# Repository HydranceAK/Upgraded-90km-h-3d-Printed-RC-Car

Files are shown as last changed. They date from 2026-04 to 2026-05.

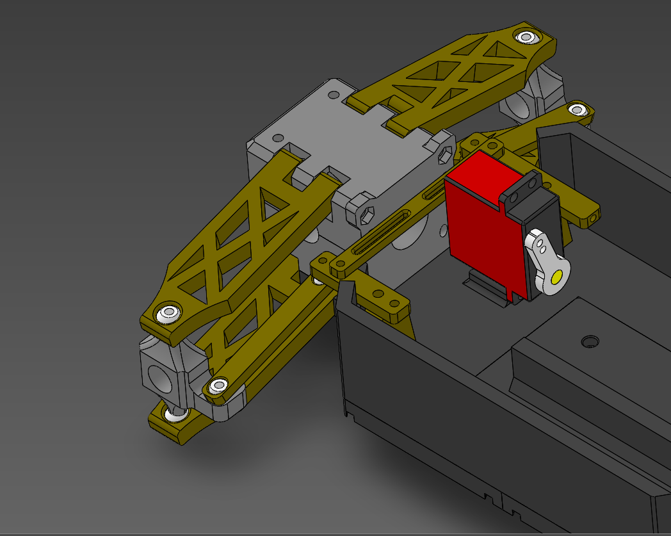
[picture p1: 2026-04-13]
Images/Screenshot 2026-04-12 164648.png

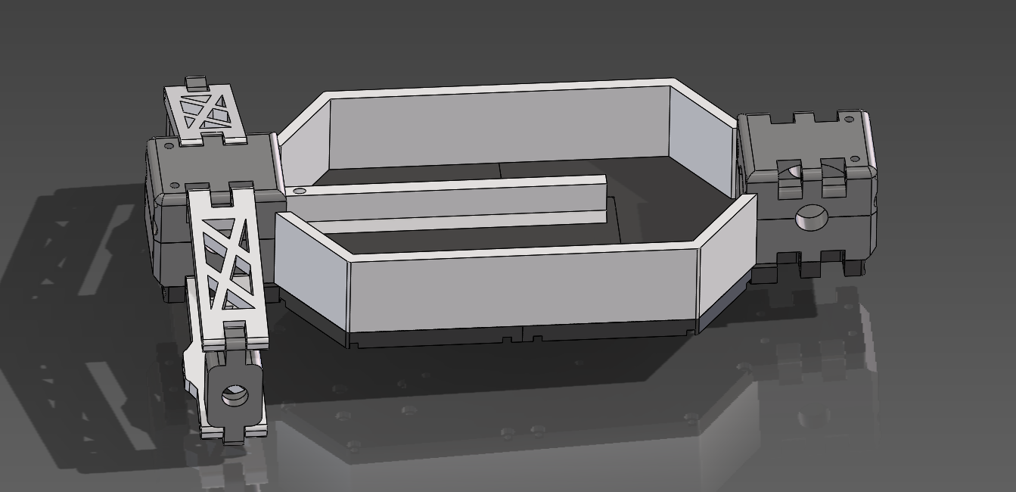
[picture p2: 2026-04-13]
Images/Screenshot 2026-04-11 005427.png

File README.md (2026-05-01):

Designed and engineered by Hydrance.

This is my final and best version of my 3d printed RC Car series. Upgraded with metal differentials, metal axles, improved suspension, 
larger frame, more space for adjustments, and an overall polished andimproved design, this will likely be my final attempt at making the perfect 3d printed RC Car.  

Im making this project because my previous build, the 60km/h RC Car, is too weak and the gears snap under high load. This makes it very annoying to drive as you need to constantly rebuild it. This new design, with the full metal drive train, should never require replacement. 

_****PROJECT STILL IN WORKS****_

Features

4WD Drivetrain

Top Speed: - 90km/h (untested as of today)

Independent Suspension

Fully metal drive train

TPU parts for flexible components (tires, dampening mounts, impact zones)

PETG parts for strong structural elements (chassis, arms, mounts)

**Printing Notes**

TPU recommended for flexible and shock-absorption components

PETG recommended for strength, heat resistance, and rigidity

Everything can be printed on Bambu Lab a1 (0.4 or 0.6 nozzle)

Hardware, electronics, and drivetrain components sourced Amazon and AliExpress

**Disclaimer**

This project is provided for personal use only.

You may not sell, redistribute, upload, or copy this design without direct permission from the creator.

I am not responsible for any damage, injury, or misuse involving this design, its assembly, or its operation.

Operate RC vehicles safely and responsibly.

**Contact**

For permissions, questions, or collaboration, contact me at:

Email: abdusamaku@gmail.com

YouTube: https://youtube.com/@HydranceYT







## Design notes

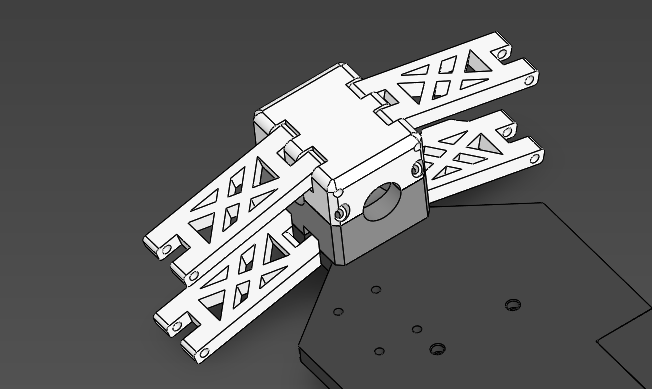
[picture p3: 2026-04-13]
Images/Screenshot 2026-04-10 205925.png

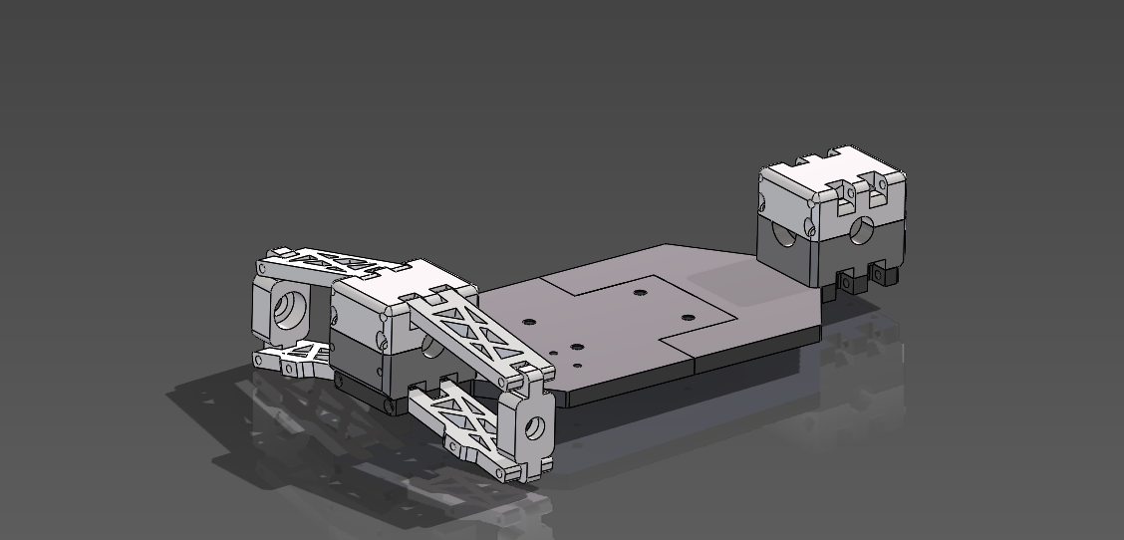
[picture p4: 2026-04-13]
Images/Screenshot 2026-04-10 213503.png

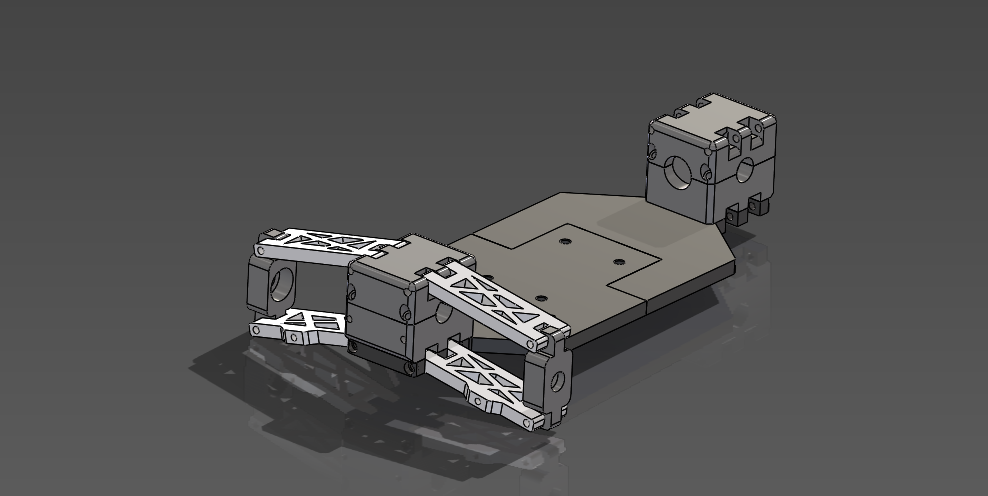
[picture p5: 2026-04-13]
Images/Screenshot 2026-04-10 213638.png

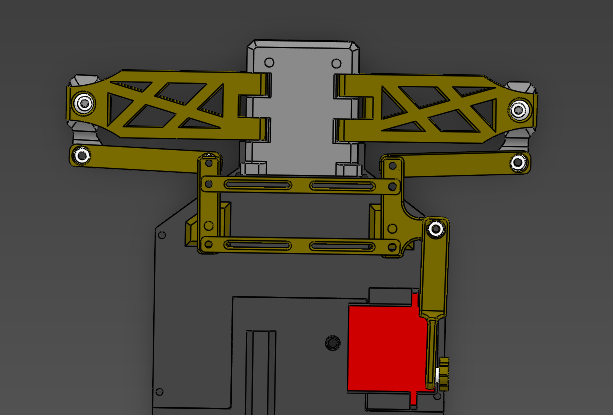
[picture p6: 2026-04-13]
Images/Screenshot 2026-04-12 174644.png

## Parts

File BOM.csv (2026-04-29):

Part Name | Quantity | Link | Link 2 | Unit Price (cheaper of the two links) | Total
HSP 1:10 RC Car Front Differential Gearbox Assembly for 94111 94123 02051 02030 03015 Models | 1 | https://www.aliexpress.com/item/32785144165.html | https://www.aliexpress.com/item/1005011988428927.html | $11.50 | $11.50
HSP 1:10 RC Car Rear Differential Gearbox Assembly Upgrade Set for 94111 94123 02051 02030 03015 Model | 1 | https://www.aliexpress.com/item/32785144165.html | https://www.aliexpress.com/item/1005011988428927.html | $12.50 | $12.50
HSP 166015 Universal Drive Joint Shaft For 1/10th | 2 | https://www.aliexpress.com/item/33063155396.html | https://www.aliexpress.com/item/1005008845154443.html | $8.00 | $16.00
Hex Mounts (12mm, 9mm thickness) | 1 | https://www.aliexpress.com/item/4001100802918.html |  | $6.00 | $6.00
170mm Central Drive Shaft With Cups | 1 | https://www.aliexpress.com/item/1005002029883656.html | https://www.aliexpress.com/item/1005004008554769.html | $6.00 | $6.00
Spur Gears (21T & 64T) 11184 Steel Metal Spur HSP Car | 1 | https://www.aliexpress.com/item/4000545586084.html | https://www.aliexpress.com/item/1005008726909208.html | $5.00 | $5.00
Motor (2850KV 3670) 3-4S Lipos | 1 | https://www.amazon.ca/GoolRC-S3670-2850KV-Brushless-Sensorless/dp/B08YD792LM |  | $50.00 | $50.00
ESC (120A) 2-3s (60km/h) 2-4s (100km/h) | 1 | https://www.amazon.ca/Brushless-Programmable-Brushed-Banana-Female/dp/B09YQ7YGJF | https://www.amazon.ca/XC-Sensorless-Brushless-Continuous-Applicable/dp/B0FY5QHQQJ | $30.00 | $30.00
Threaded Inserts (m2, m3, m4 sets) | 1 | https://www.amazon.ca/Heat-Set-Threaded-Inserts-Printing-Components/dp/B0DCJ4MXCM |  | $14.00 | $14.00
M4 Screw Assortment | 1 | https://www.amazon.ca/Hilitchi-300-Piece-Phillips-Assortment-stainless/dp/B01N4HPO2D |  | $12.00 | $12.00
M3 Screw Assortment | 1 | https://www.amazon.ca/gp/product/B01NBOCXHE |  | $12.00 | $12.00
INJORA RC Transmitter 2.4GHz 6CH Controler and Receiver | 1 | https://www.amazon.ca/INJORA-Transmitter-Controler-Receiver-Crawler/dp/B08SJW1TMC | https://www.aliexpress.com/item/1005005214765667.html | $30.00 | $30.00
3s LIPO PURCHASE 4S FOR HIGHER POWER | 1 | https://www.amazon.ca/Zeee-Connector-Airplane-Helicopter-Quadcopter/dp/B0BZ46JRGJ | https://www.aliexpress.com/item/1005009205837699.html | $20.00 | $20.00
Servo Motor (20kg) MG996R | 1 | https://www.amazon.ca/dp/B0769DFJVK |  | $25.00 | $25.00
 |  |  |  |  | $250.00

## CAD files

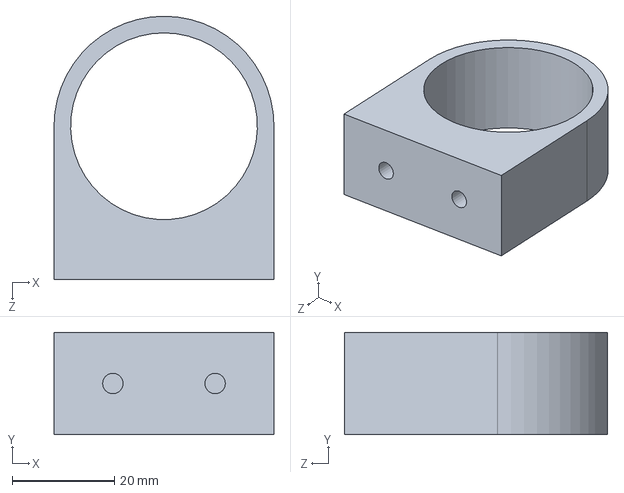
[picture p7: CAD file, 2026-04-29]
Solidworks Files/Motor-Support.SLDPRT
43.0 x 20.0 x 51.5 mm

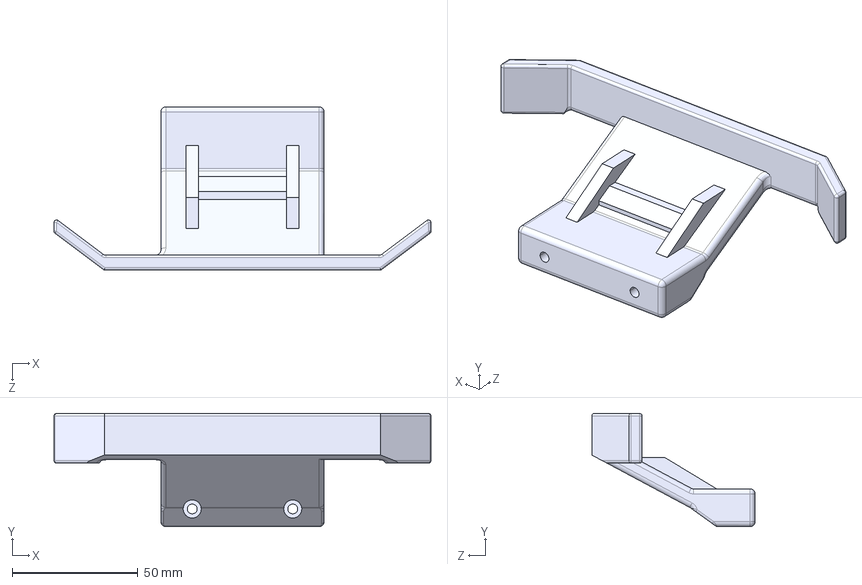
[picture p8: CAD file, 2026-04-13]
STEP Files/Upgraded Bumper.STEP
150.0 x 45.0 x 65.0 mm

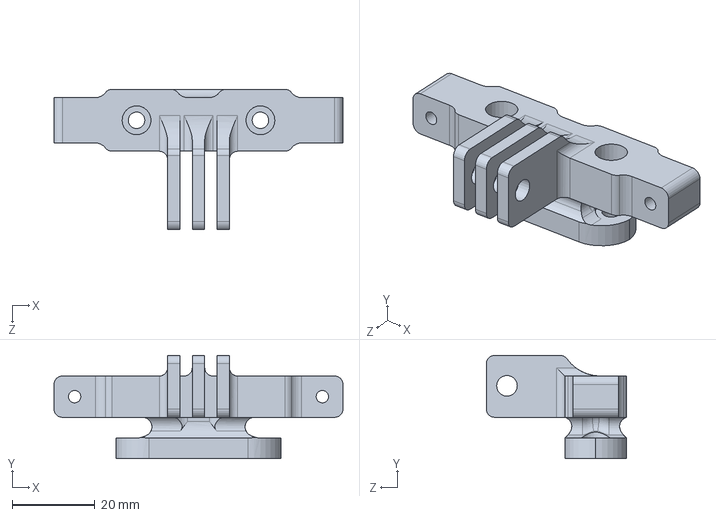
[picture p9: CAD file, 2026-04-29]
Solidworks Files/Shock-Mount.SLDPRT
70.0 x 25.0 x 34.0 mm

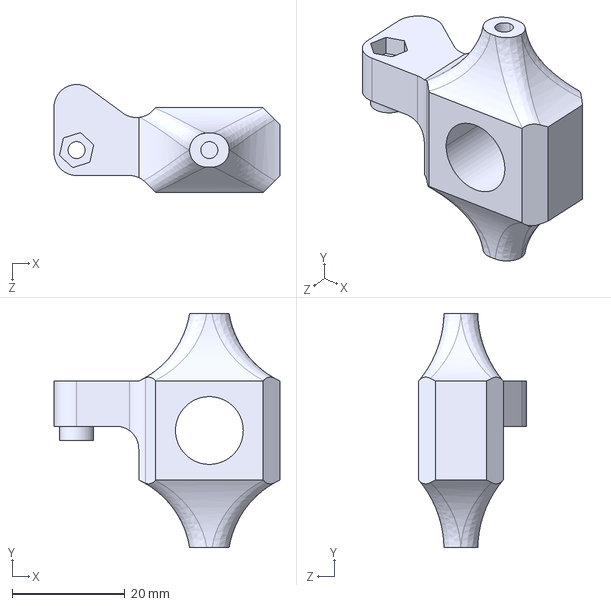
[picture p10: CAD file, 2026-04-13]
STEP Files/Front-Wheel-Hub-Left.STEP
40.0 x 41.5 x 19.1 mm

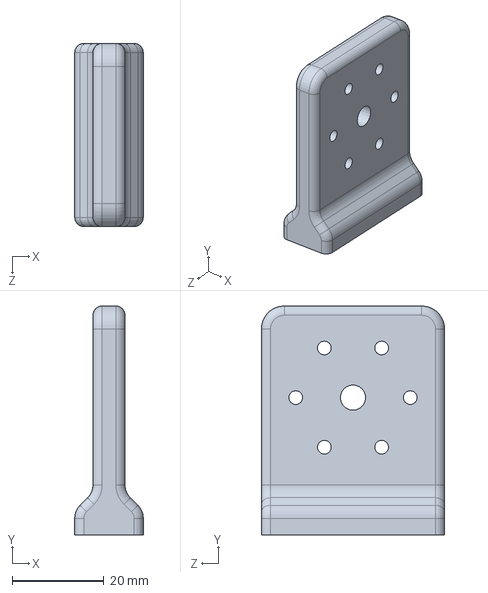
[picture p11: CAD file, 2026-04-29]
Solidworks Files/Motor-Mount.SLDPRT
15.0 x 50.0 x 40.0 mm

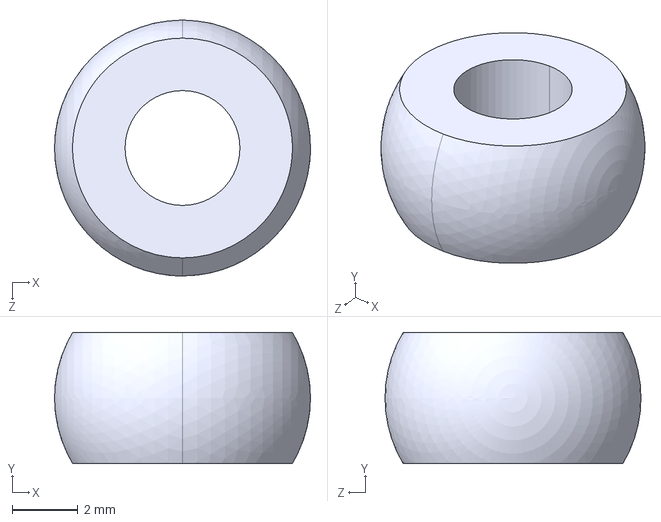
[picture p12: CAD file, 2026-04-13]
STEP Files/Steering-Ball.STEP
7.80 x 4.00 x 7.80 mm

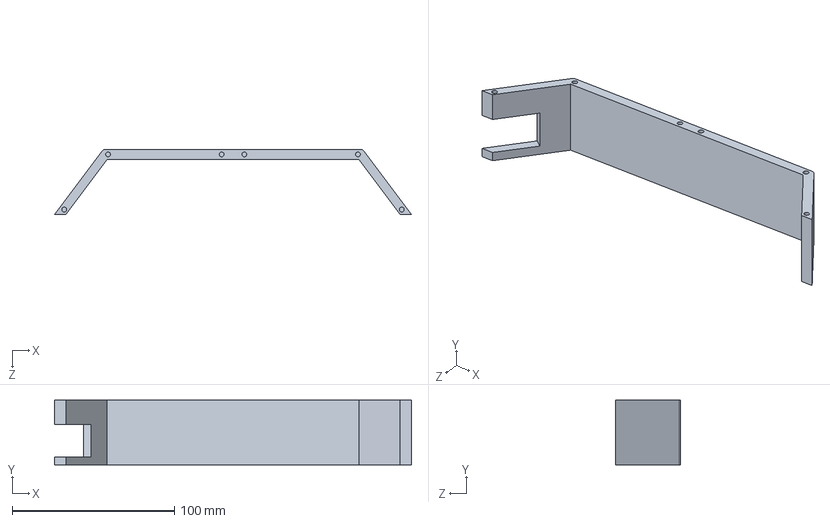
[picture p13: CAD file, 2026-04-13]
Solidworks Files/Frame Railing.SLDPRT
220.0 x 40.0 x 40.0 mm

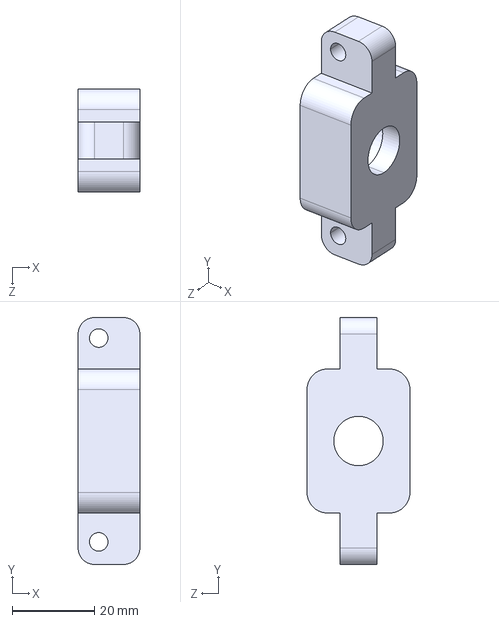
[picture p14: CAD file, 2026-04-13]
STEP Files/Rear-Wheel-Hub.STEP
15.0 x 60.0 x 25.0 mm

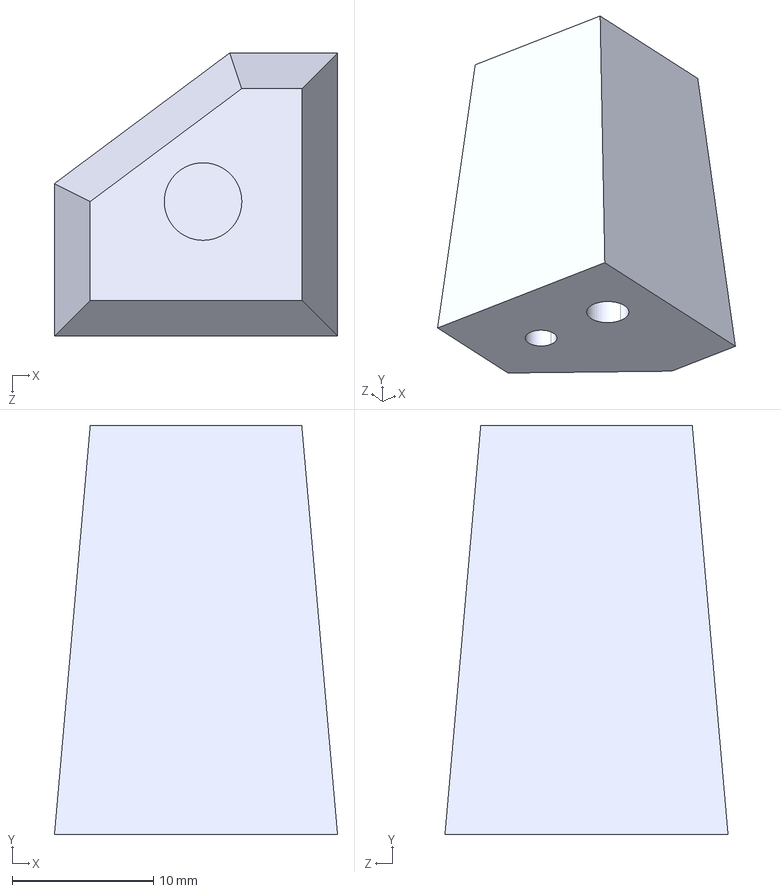
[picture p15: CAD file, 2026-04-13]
STEP Files/Steering-Post-Left.STEP
20.1 x 29.0 x 20.1 mm

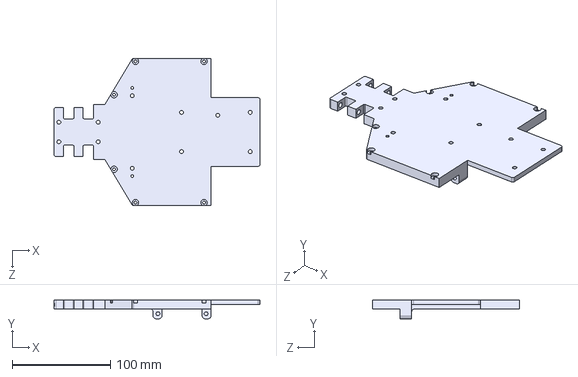
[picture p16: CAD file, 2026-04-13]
STEP Files/Frame-Front.STEP
210.0 x 19.0 x 150.0 mm

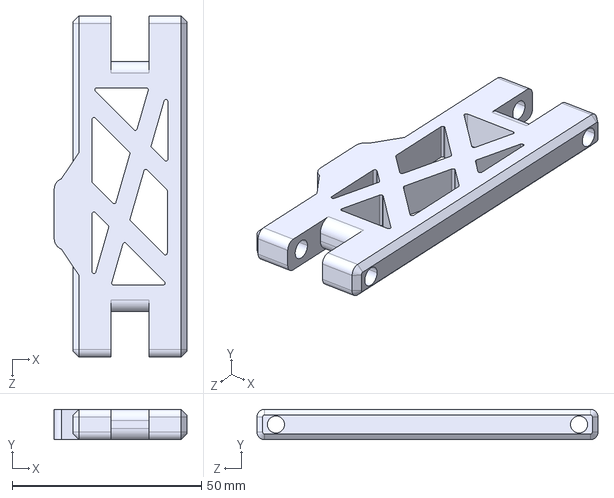
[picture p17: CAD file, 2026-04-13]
STEP Files/Rear-Bottom-Suspension-Arm.STEP
35.0 x 8.00 x 90.0 mm

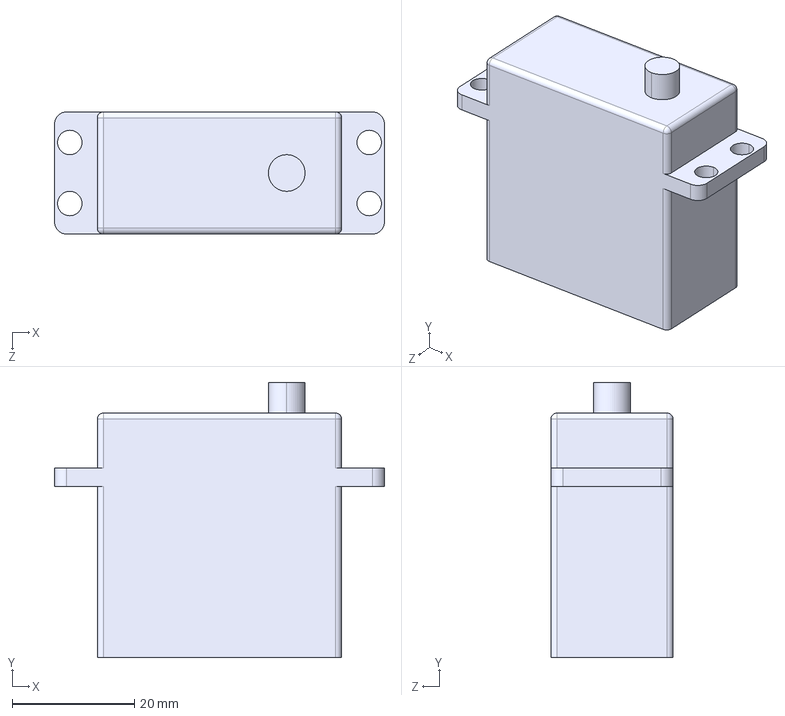
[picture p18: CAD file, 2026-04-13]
STEP Files/ServoMotor.STEP
54.0 x 45.0 x 20.0 mm

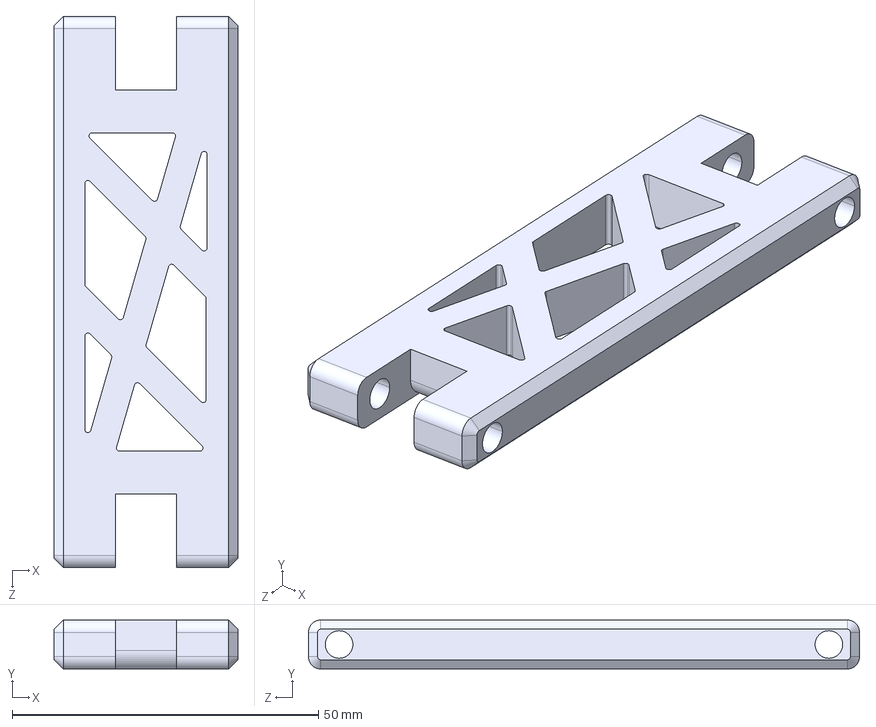
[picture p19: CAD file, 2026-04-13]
STEP Files/Rear-Top-Suspension-Arm.STEP
30.0 x 8.00 x 90.0 mm

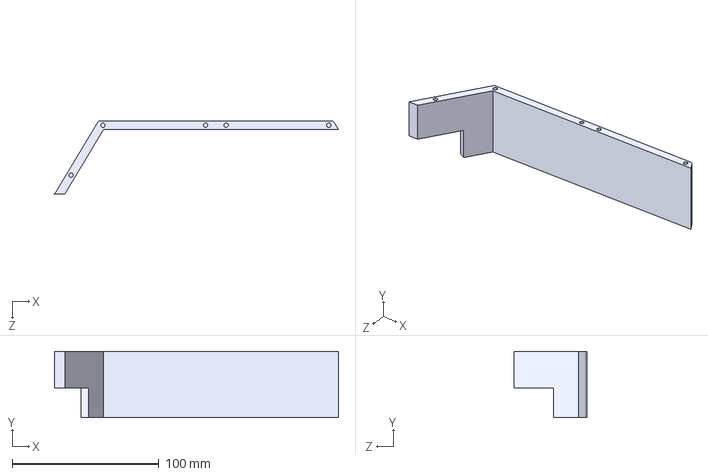
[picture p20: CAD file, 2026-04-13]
STEP Files/Frame-Railing-Left.STEP
193.6 x 45.0 x 50.0 mm

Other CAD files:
STEP Files/Main Assembly.STEP
STEP Files/Steering-Arm.STEP
STEP Files/Frame-Battery-Splitter.STEP
STEP Files/Frame-Rear.STEP
STEP Files/Battery-Stopper.STEP
STEP Files/Frame-Railing-Right.STEP
STEP Files/Frame.STEP
STEP Files/Front-Bottom-Suspension-Arm.STEP
STEP Files/Front-Suspension-Arm-Ball.STEP
STEP Files/Front-Top-Suspension-Arm.STEP
STEP Files/Front-Wheel-Hub-Right.STEP
STEP Files/Gearbox - Top.STEP
STEP Files/Gearbox.STEP
STEP Files/ServoHorn.STEP
STEP Files/Spoiler.STEP
STEP Files/Steering-Arm-Balancer.STEP
STEP Files/Steering-Arm-Post-Left.STEP
STEP Files/Steering-Arm-Post-Right.STEP
STEP Files/Steering-Ball-Servo.STEP
STEP Files/Steering-Post-Right.STEP
STEP Files/Steering-Servo-Arm-2.STEP
STEP Files/Steering-Servo-Arm.STEP
Solidworks Files/Battery-Stopper.SLDPRT
Solidworks Files/Frame-Battery-Splitter.SLDPRT
Solidworks Files/Frame-Front.SLDPRT
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

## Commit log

2026-04-13 Rename BOM For 3d Printed RC Car - Sheet1.csv to BOM.csv
    [BOM.csv]
2026-04-29 Update BOM.csv
    Added alternative links
    [BOM.csv]
2026-04-29 Add files via upload
    Updated SW Files
    [Battery-Stopper.SLDPRT, Frame-Battery-Splitter.SLDPRT, Frame-Front.SLDPRT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]
